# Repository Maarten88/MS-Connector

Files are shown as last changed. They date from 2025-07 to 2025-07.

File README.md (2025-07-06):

# MS-Connector
Design and engineering files for an open hydrofoil connector system

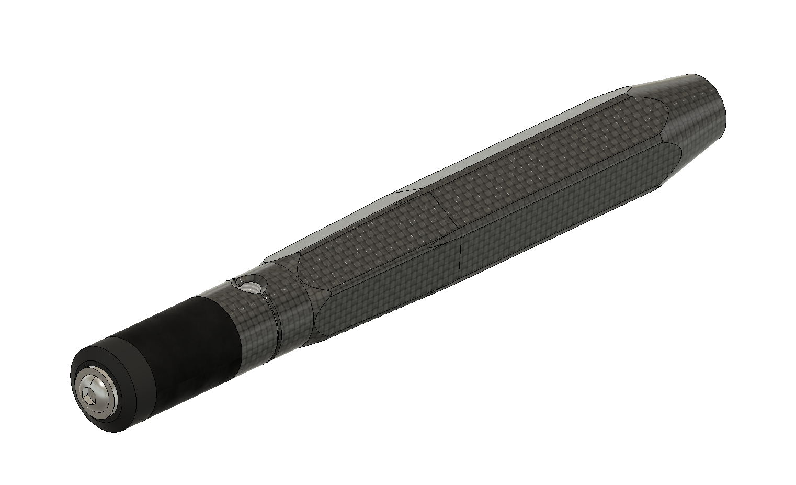
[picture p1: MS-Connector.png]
MS Connector Part


The first challenge I encountered when I started building hydrofoils was thinking up a connection system between mast, fuselage, stabilizer and front wing. After several iterations, I arrived on this system, and it has served me well for over three years now. It has proven to be strong and durable for me and several friends who are using foils I built for them. Foils that I built three years ago with this system are still perfectly fine today.

## Advantages
This connection system has several advantages over other solutions:
- Everything goes together with a single tool: a long 4 mm allen key. Assembling the foil and taking it apart is faster compared to systems that use screws.
- There are no loose screws, so loosing a screw or using the wrong one is not a thing.
- It has reasonably relaxed tolerances, and can be manufactured using the tools that I have access to at my makerspace from carbon and epoxy.[^1]
- Strong and stiff even for wide-span pump foils.
- Tolerant to salt and sand, does not corrode even when leaving assembled for a long time.
- Hydrodynamically efficient, maybe not quite as good as some race setups but still quite good.
[^1]: These tools do include a lathe, metal mill and cnc router. It would also be possible to order the metal parts and mold once from an online service. However the lathe is used for every connector made, so it is important to have.

## How does it work
This system, that I'll name the MS connector (my initials) has a 38 mm (1.5") outer diameter fuselage. This fuselage is molded rigidly to the mast, making this strong and stiff. The front foil has a connector that is pulled into the fuselage. The connector is made separately and is molded inside the front wing. Making it as a small separate part makes it easy to drill and tap the screw holes, and make it to size perfectly before the foil makes it impractical to work on.
The connector has 4 distinct parts, each part having a distinct function:
1) a straight hexagon part at 28 mm key thickness, that is molded inside the foil, sticking out 10mm to prevent wiggling loose
2) a tapered hexagon part, tapering from 28 mm back to 25mm over 60mm length. This tightens the foil inside the fuselage and transfers the load.
3) a 25 mm round part, 20 mm long. In the middle is a grub screw that is used as extra lock.
4) a 25 mm round rubber cylinder, 40 mm long, that runs over a "reverse taper" inside, with an end cap and a flathead screw on the end. The inner diameter tapers out from 14 mm to 16 mm.

The fuselage has a cavity that matches the connector shape. After inserting the connector into the fuselage, a long allen key coming in from the back is used to tighten the screw and compress the rubber cylinder. This expands against the inner wall, then the reverse taper will pull the connector in, firmly tightening the tapered part. Then the grub screw is tightened, it will push against the wall, preventing the connector from falling out even if the primary mechanism slips or fails.
The tapered part will make a very tight connection, it will not come loose easily. When disassembling, first loosen up the grub screw, then loosen the end cap screw. Inside the fuselage there is a hole in the center that the allen key fits through (making it easy to find the screw), but the hole is smaller than the screw head. Reversing the screw until the head hits the internal hole, that will push the foil out from its tight fit without much force.

## Stabilizer connection
For the stabilizer connection, a 25 mm carbon round tube is used. It is placed in line with the front wing and slides in after the front wing is attached. Because it slides and is fixed with set screws, the stabilizer length can be adjusted. The set screws are 22.5 mm apart, two or three small holes in the fuselage 45 mm apart are used to screw these in. In the center of the carbon tube is SRFB/Tufnol rod, for M8 threaded holes. This system was actually not designed by me, it was created by Woody Cookie from Scheveningen and I like this design. The round shape requires the user to set it horizontally by hand before tightening the screws, but the advantage is that sand does not lock up the mechanism.

## Screws
Note M8 set screws (ISO 4027) and M6 flange screws (ISO 7380-2) both fit a 4 mm allen key. That is why these are used throughout.

## Manufacturing
For manufacturing this, I use two aluminium metal parts that are molded in when making the fuselage. 
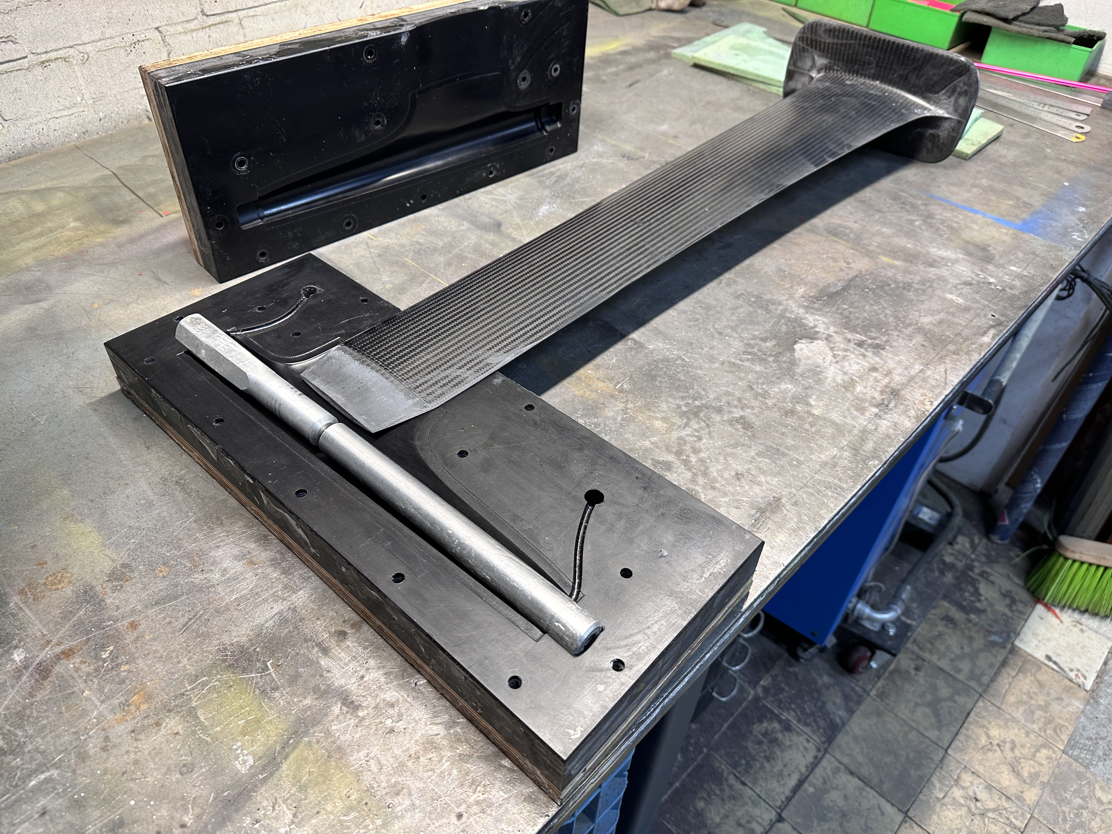
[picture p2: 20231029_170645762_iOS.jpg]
Alu inserts before fuselage molding


After demolding the fuselage, I leave the aluminium parts inside and post-cure the mast/fuselage at 60 degrees for 6 hours (consistent with the epoxy manufacturer guidelines). This makes the aluminium expand during post-cure, after cooling down the aluminium parts are pulled out easily using a pully and M16 screw. This creates a cavity that precisely matches the connector, with 0.1 mm play for sand.
Demolded fuselage with alu inserts

For the connector that is actually going into the front wing I use a mold that is made from 25 mm thick HPL (Trespa brand) plastic using a CNC router. In the center I use a 6 mm wooden stick connected to a 80mm SRBF (Tufnol) rod (10 mm diameter) at the threaded end part. This center is tightly wrapped in carbon (0 and 45 degrees) and infused under vacuum. The 28 mm hexagon from sold carbon fiber should be plenty strong to carry the load of a front wing. After it is demolded, it is post processed on the lathe to make the circular part perfectly round and tap a long M6 thread in the center.

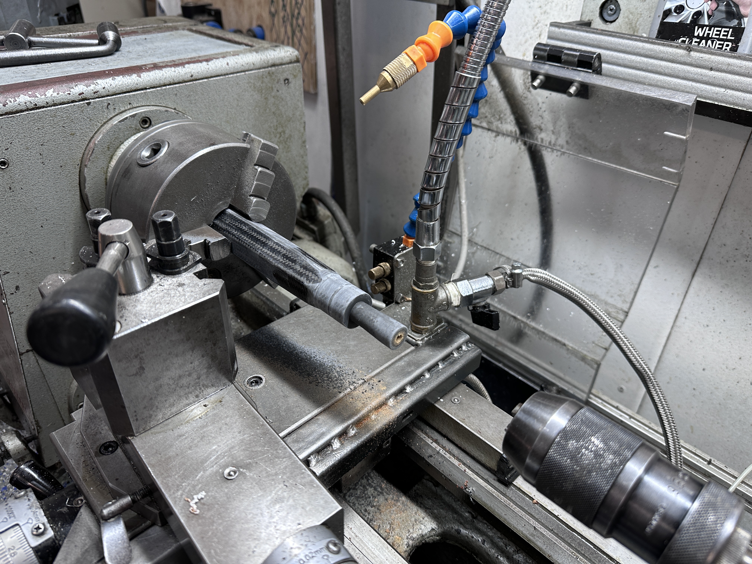
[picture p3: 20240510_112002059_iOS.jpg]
Making to size on the lathe


After the connector part is drilled and tapped, it is molded inside a front wing.
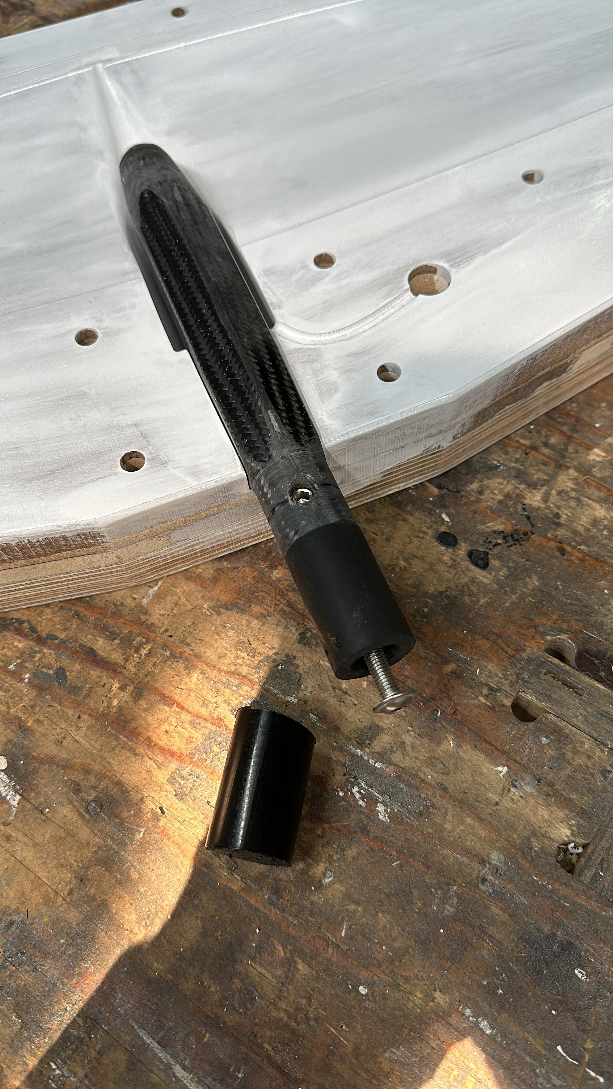
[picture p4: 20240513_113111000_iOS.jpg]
Molding the connector part in a foil


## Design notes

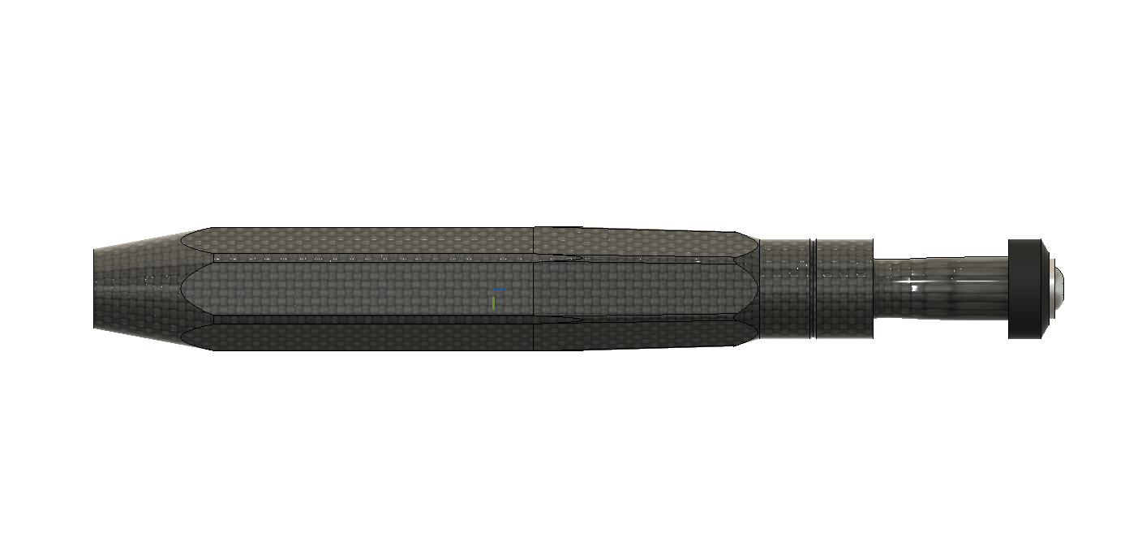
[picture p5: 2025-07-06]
MS-Connector-Screw.png

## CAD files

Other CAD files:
MS-Connector-mold.f3z
MS-Connector.f3d

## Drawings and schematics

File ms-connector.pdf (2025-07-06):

28 | 28 | Ø31 M8x1.25 6H x 15/20 M16x2 6H x 40/50

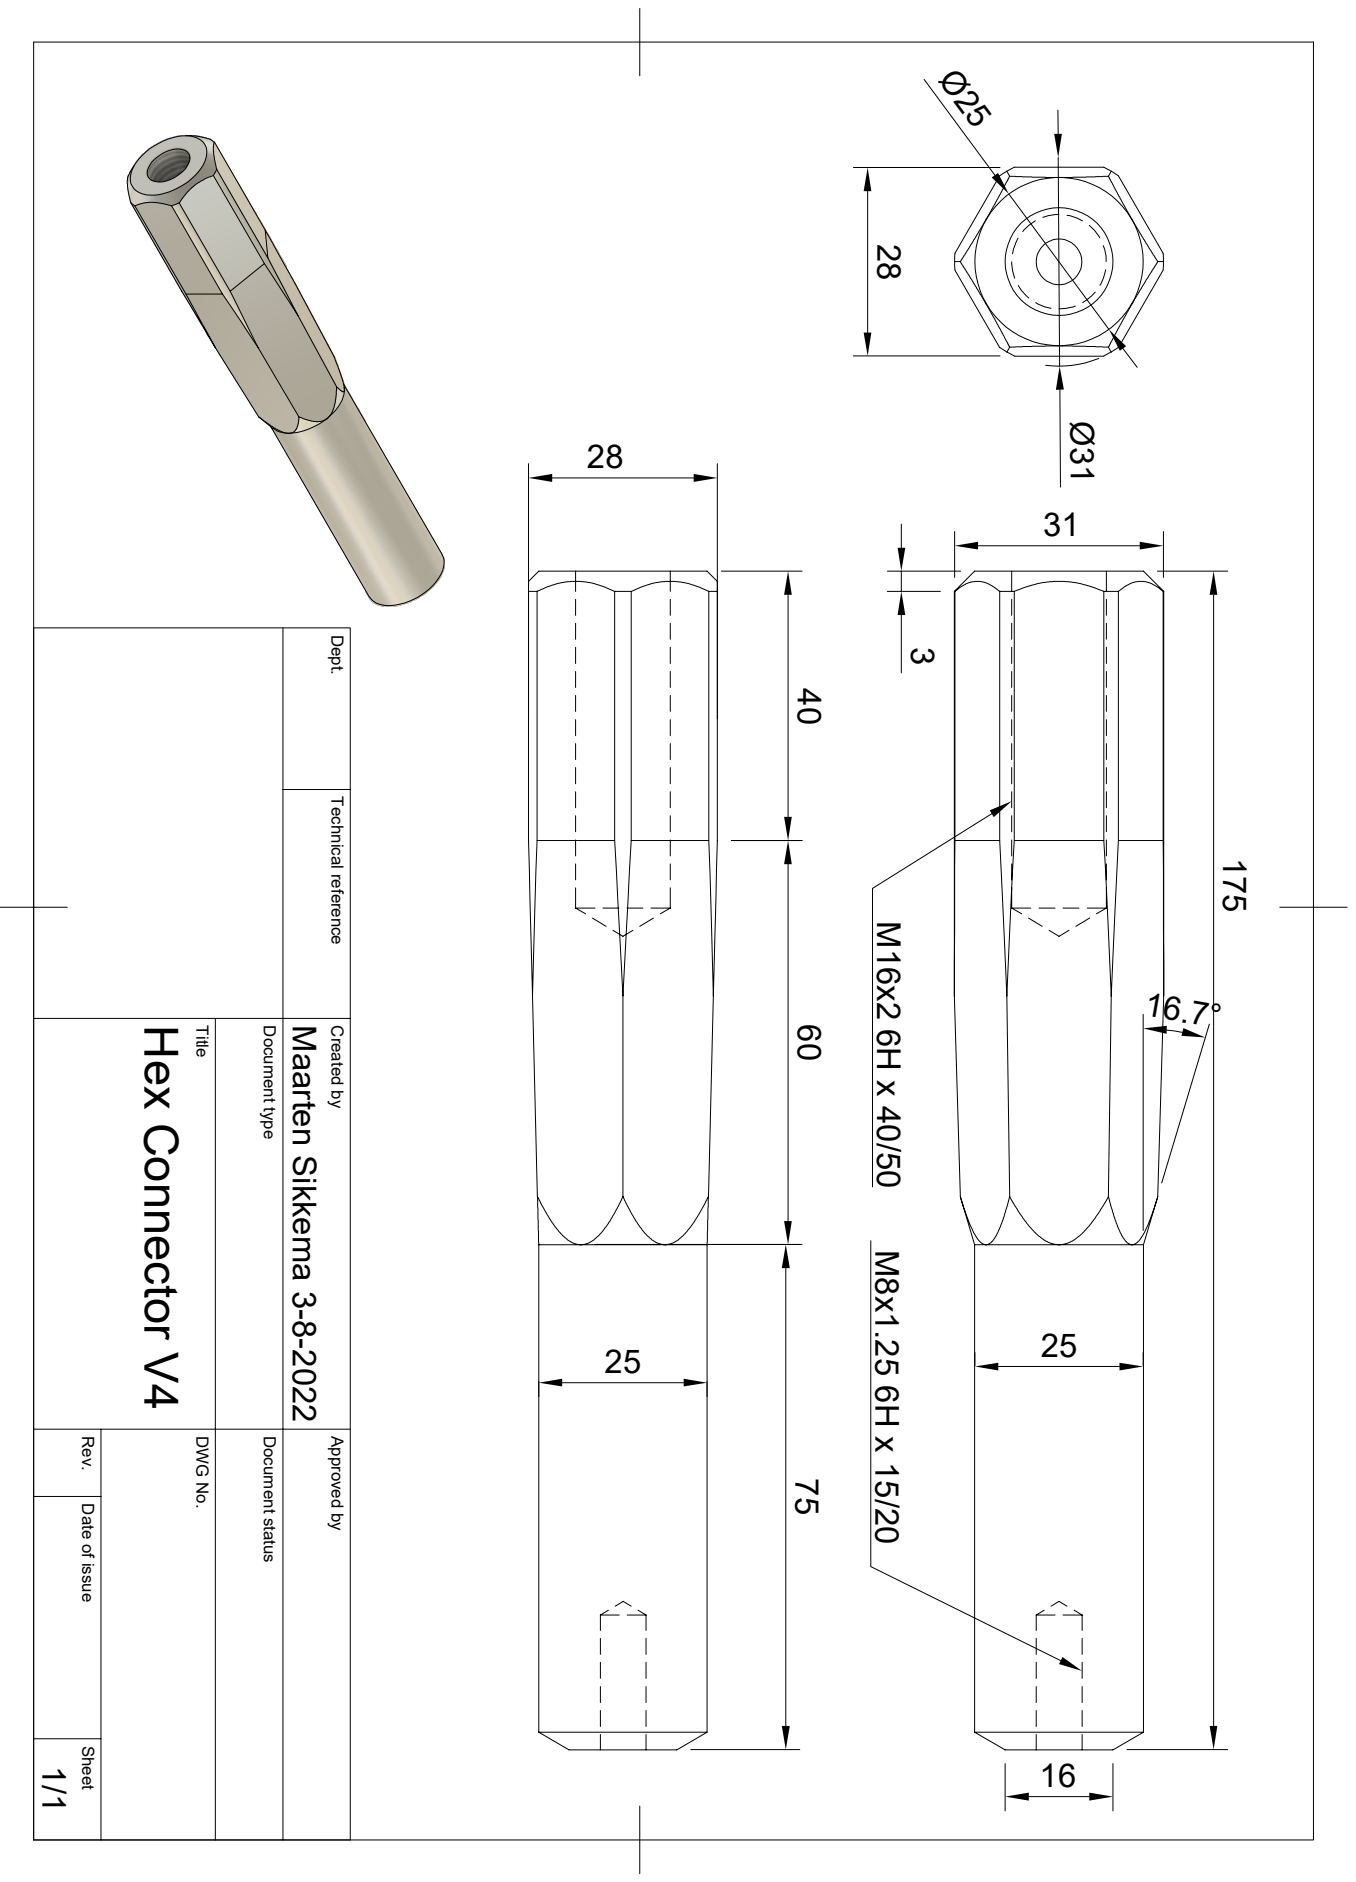
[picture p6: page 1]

Dept. Technical reference Created by Approved by Title DWG No. Document type Document status Rev. Date of issue Sheet 3-8-2022 1/1 Hex Connector V4 Maarten Sikkema 175 40 60 75
